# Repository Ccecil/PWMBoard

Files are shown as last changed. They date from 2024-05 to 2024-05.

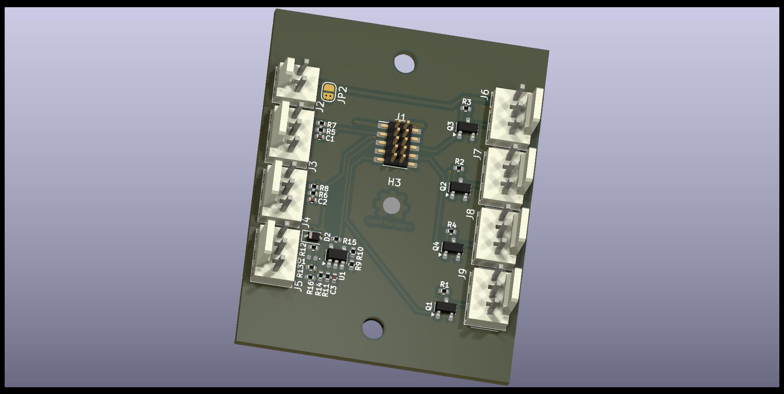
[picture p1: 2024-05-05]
PWMlaserBoardTop.jpg

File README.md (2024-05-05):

PWMlaserBoardTop

This board is to be used to expand the PWM header from a V2 Smoothieboard (or Gadgeteer) header.  

- 4 mosfet buffered PWM outputs with jumper options to select between Pullup voltages and/or disable the pullup resistor for Opendrain outputs.
- 2 Switch inputs which are debounced with passives and have optional pullup resistor/voltage.
- 1 Comparator probe input which increases the repeatability of probes and allows use of probe voltages from 3-45v (through jumper configs)
- Optional voltage input for using higher voltages on the PWM output pin3 (i.e. Running higher voltages to the servo motor or using different 5v source)

Comparator probe input jumper options

- J5 pin 3 input voltage set to
- 2.9v-5v (default)
- 5-24v (JP5-2 cut)
- 6-45v (JP5-2 and JP5-3 cut)

PWM output and Switch input jumpers.

- JP2: J6-J9 pin 3 optional voltage source select (J1 Pin 2 default, cut to use J2 Pin 1)
- JP3-1: J3 pin 1 and pin 3 pullup Voltage select
- JP3-2: J3 pin 3 pullup disable
- JP4-1: J4 pin 1 and pin 3 pullup Voltage select
- JP4-2: J4 pin 3 pullup disable
- JP5-1: J5 pin 1 Voltage select
- JP5-2: J5 pin 3 pullup cut (required for HV operation)
- JP5-3: J5 pin 3 Low/High voltage select (default low)
- JP6: J6 pin 1 pullup Voltage select
- JP7: J7 pin 1 pullup Voltage select
- JP8: J8 pin 1 pullup Voltage select
- JP9: J9 pin 1 pullup Voltage select

Jumper and connector numbers match their respective driving pin from the J1 header

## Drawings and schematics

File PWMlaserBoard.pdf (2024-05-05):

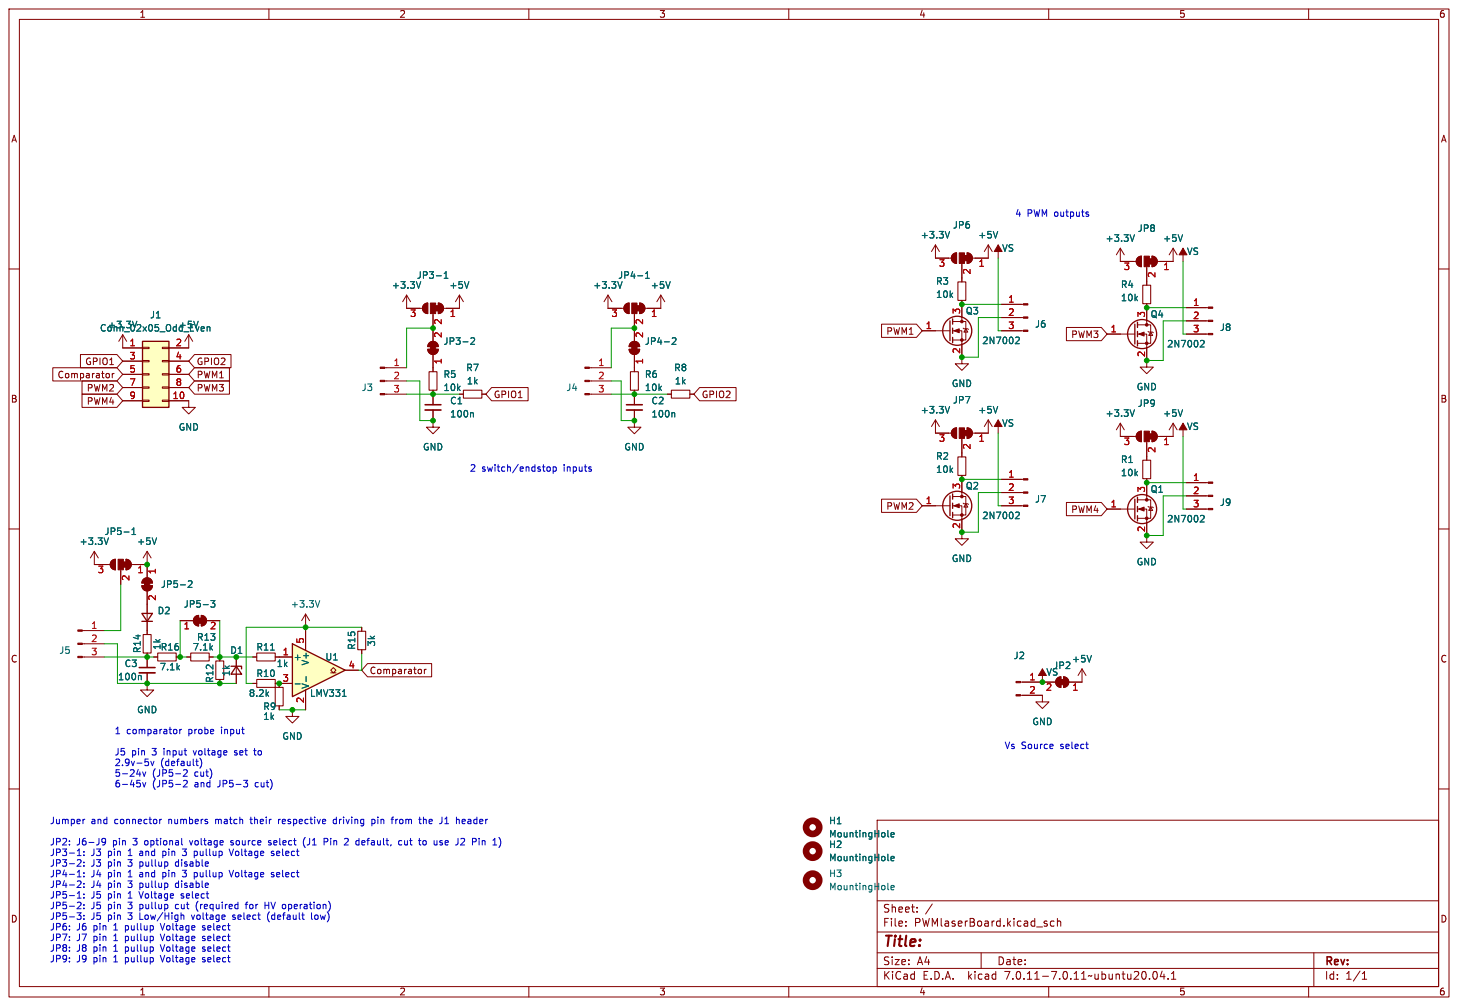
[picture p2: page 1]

Id: 1/1 Title: File: PWMlaserBoard.kicad_sch Sheet: /

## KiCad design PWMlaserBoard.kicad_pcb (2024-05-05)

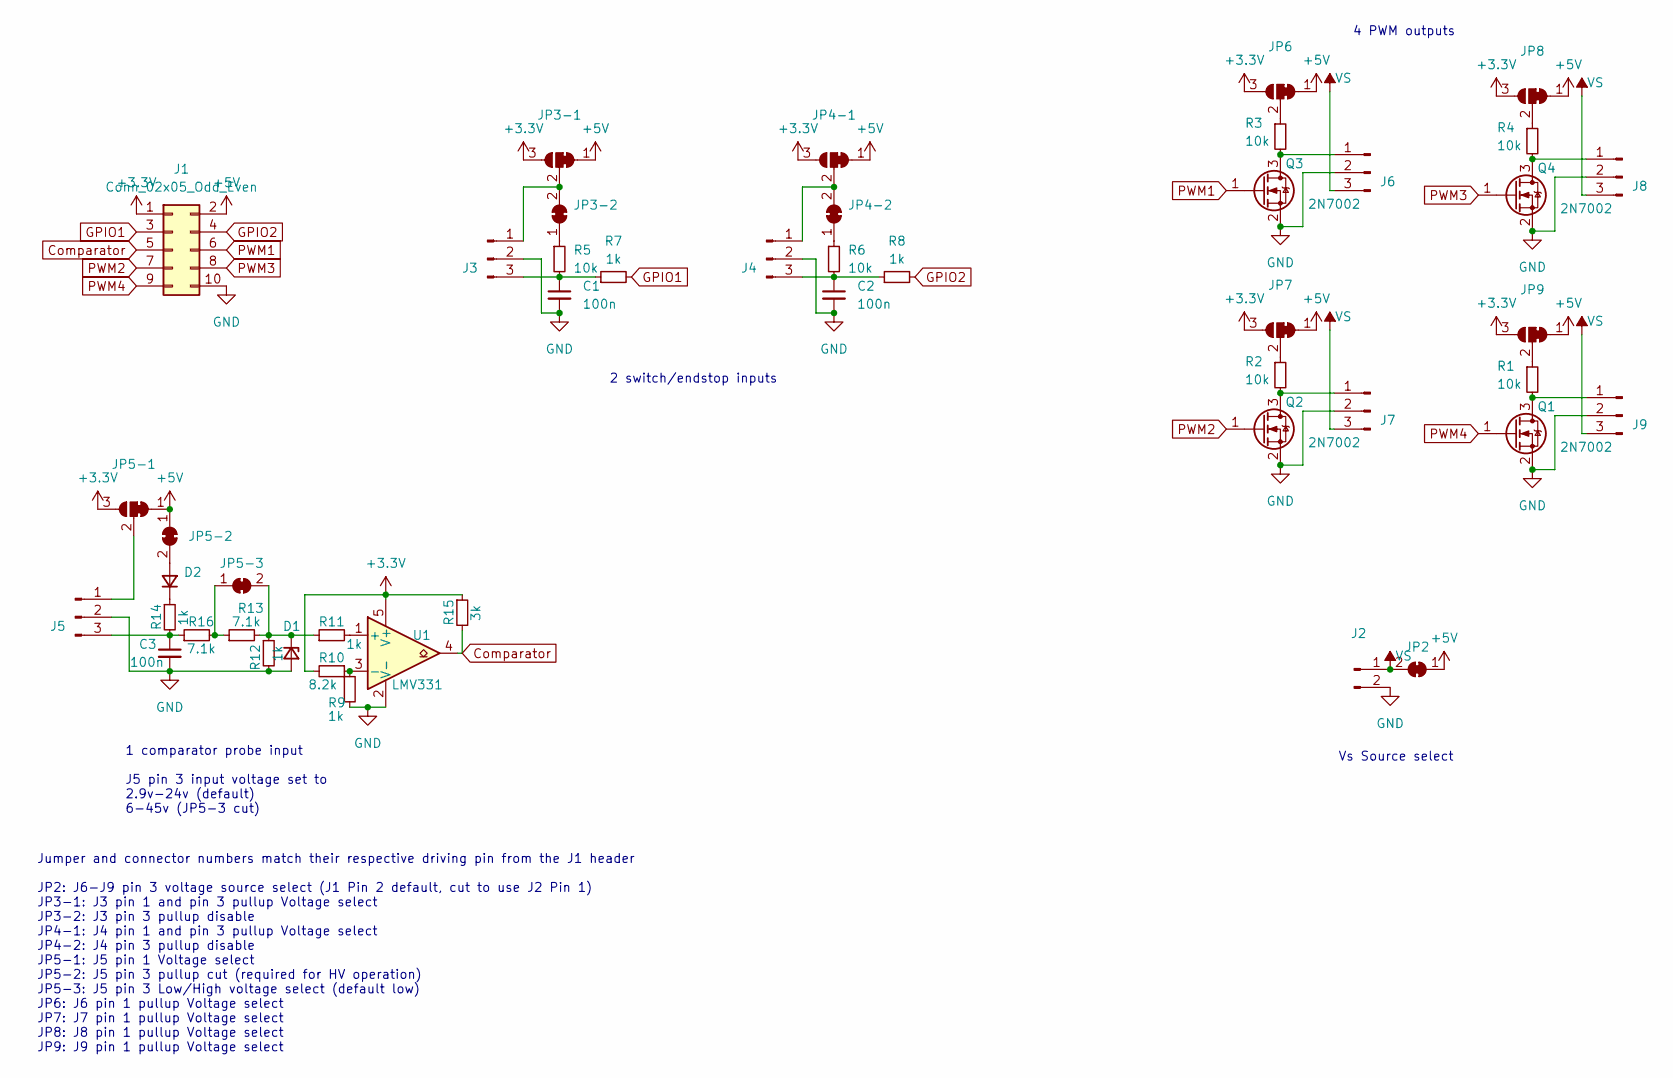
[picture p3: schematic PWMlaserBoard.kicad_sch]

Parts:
C1, C2, C3: 100n; C_0402_1005Metric
D1: D_Zener_Small; D_0402_1005Metric
D2: D_Small; D_SOD-323
J1: Conn_02x05_Odd_Even; PinHeader_2x05_P1.27mm_Vertical_SMD
J2: Conn_01x02_Pin; Molex_KK-254_AE-6410-02A_1x02_P2.54mm_Vertical
J3, J4, J5, J6, J7, J8, J9: Conn_01x03_Pin; Molex_KK-254_AE-6410-03A_1x03_P2.54mm_Vertical
JP2, JP3-2, JP4-2, JP5-2, JP5-3: SolderJumper_2_Bridged; SolderJumper-2_P1.3mm_Bridged_RoundedPad1.0x1.5mm
JP3-1, JP4-1, JP5-1, JP6, JP7, JP8, JP9: SolderJumper_3_Bridged12; SolderJumper-3_P1.3mm_Bridged12_RoundedPad1.0x1.5mm
Q1, Q2, Q3, Q4: 2N7002; SOT-23
R1, R2, R3, R4, R5, R6: 10k; R_0402_1005Metric
R7, R8, R9, R11, R12, R14: 1k; R_0402_1005Metric
R10: 8.2k; R_0402_1005Metric
R13, R16: 7.1k; R_0402_1005Metric
R15: 3k; R_0402_1005Metric
U1: LMV331; SOT-23-5

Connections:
+3.3V: J1.1, JP3-1.3 (B), JP4-1.3 (B), JP5-1.3 (B), JP6.3 (B), JP7.3 (B), JP8.3 (B), JP9.3 (B), R10.2, R15.1, U1.5 (V+)
+5V: J1.2, JP2.1 (A), JP3-1.1 (A), JP4-1.1 (A), JP5-1.1 (A), JP5-2.1 (A), JP6.1 (A), JP7.1 (A), JP8.1 (A), JP9.1 (A)
Comparator: J1.5, R15.2, U1.4
GND: C1.2, C2.2, C3.2, D1.2 (A), J1.10, J2.2, J3.2, J4.2, J5.2, J6.2, J7.2, J8.2, J9.2, Q1.2 (S), Q2.2 (S), Q3.2 (S), Q4.2 (S), R9.2, R12.2, U1.2 (V-)
GPIO1: J1.3, R7.2
GPIO2: J1.4, R8.2
unnamed: D1.1 (K), JP5-3.2 (B), R11.1, R12.1, R13.2
unnamed: D2.2 (A), JP5-2.2 (B)
unnamed: D2.1 (K), R14.1
unnamed: J3.1, JP3-1.2 (C), JP3-2.2 (B)
unnamed: C1.1, J3.3, R5.2, R7.1
unnamed: J4.1, JP4-1.2 (C), JP4-2.2 (B)
unnamed: C2.1, J4.3, R6.2, R8.1
unnamed: J5.1, JP5-1.2 (C)
unnamed: C3.1, J5.3, R14.2, R16.1
unnamed: J6.1, Q3.3 (D), R3.2
unnamed: J7.1, Q2.3 (D), R2.2
unnamed: J8.1, Q4.3 (D), R4.2
unnamed: J9.1, Q1.3 (D), R1.2
unnamed: JP3-2.1 (A), R5.1
unnamed: JP4-2.1 (A), R6.1
unnamed: JP5-3.1 (A), R13.1, R16.2
unnamed: JP6.2 (C), R3.1
unnamed: JP7.2 (C), R2.1
unnamed: JP8.2 (C), R4.1
unnamed: JP9.2 (C), R1.1
unnamed: R11.2, U1.1 (+)
unnamed: R9.1, R10.1, U1.3 (-)
PWM1: J1.6, Q3.1 (G)
PWM2: J1.7, Q2.1 (G)
PWM3: J1.8, Q4.1 (G)
PWM4: J1.9, Q1.1 (G)
VS: J2.1, J6.3, J7.3, J8.3, J9.3, JP2.2 (B)

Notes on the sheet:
4 PWM outputs
Vs Source select
2 switch/endstop inputs
Jumper and connector numbers match their respective driving pin from the J1 header JP2: J6-J9 pin 3 voltage source select (J1 Pin 2 default, cut to use J2 Pin 1) JP3-1: J3 pin 1 and pin 3 pullup Voltage select JP3-2: J3 pin 3 pullup disable JP4-1: J4 pin 1 and pin 3 pullup Voltage select JP4-2: J4 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
1 comparator probe input J5 pin 3 input voltage set to 2.9v-24v (default) 6-45v (JP5-3 cut)

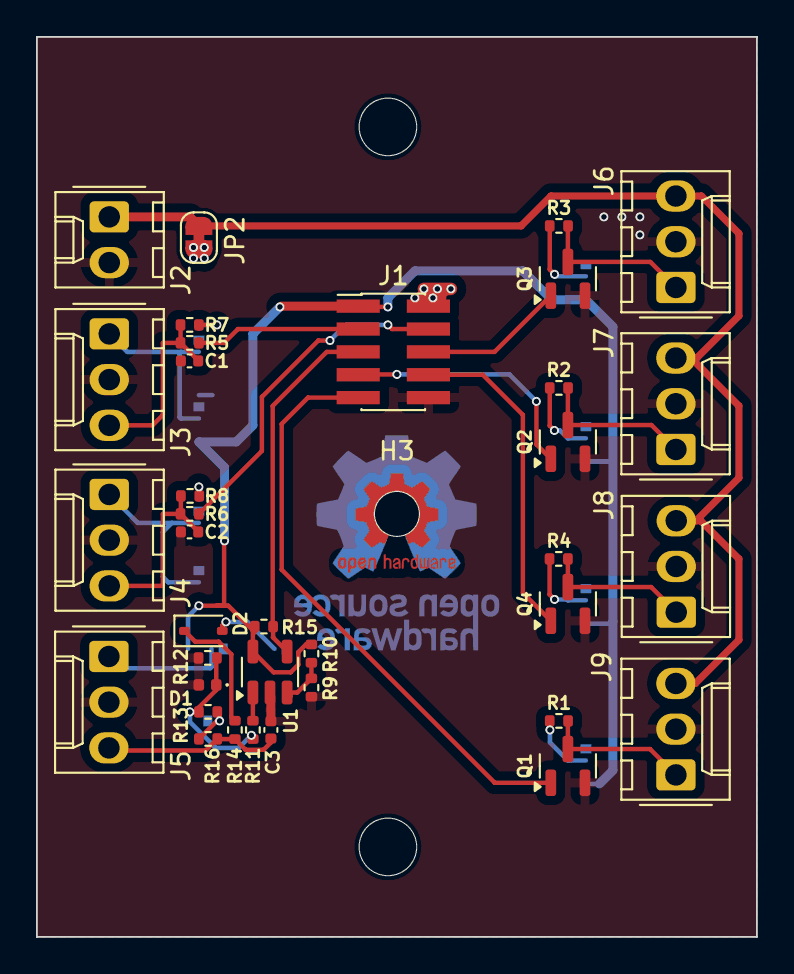
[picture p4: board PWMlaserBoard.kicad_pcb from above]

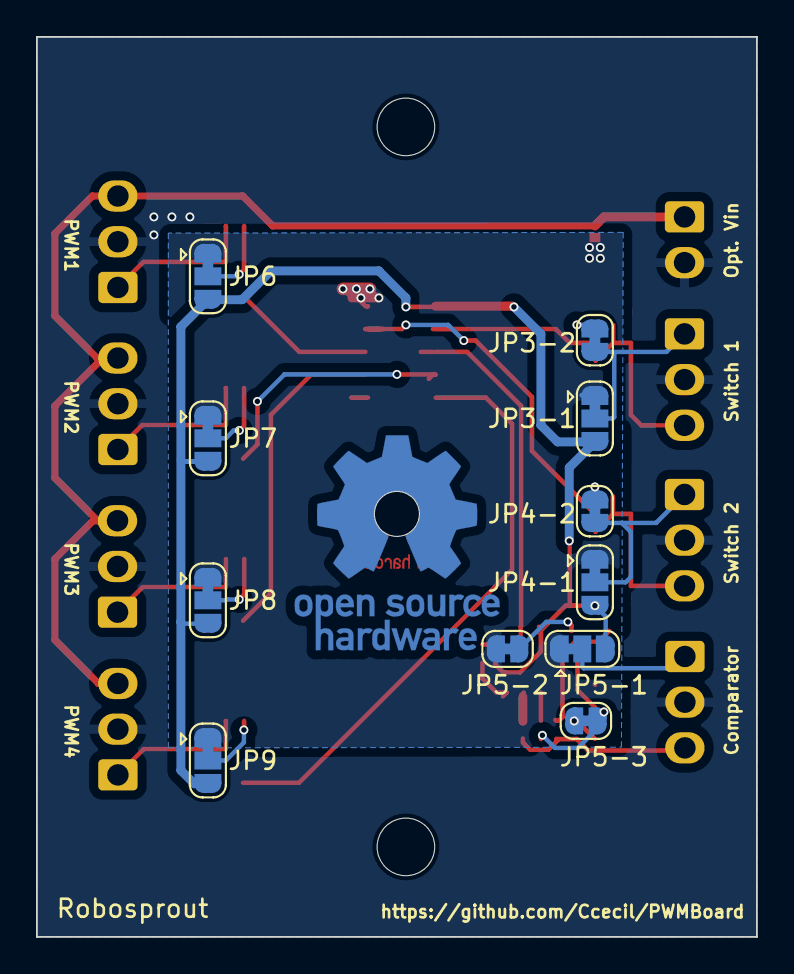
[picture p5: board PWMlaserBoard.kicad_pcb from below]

Board: 2 copper layers, 40.0 x 50.0 mm, 50 parts (11 on the bottom side), 33 nets.

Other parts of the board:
H1, H2: MountingHole; MountingHole_3.2mm_M3
H3: StencilHole; MountingHole_2.5mm
